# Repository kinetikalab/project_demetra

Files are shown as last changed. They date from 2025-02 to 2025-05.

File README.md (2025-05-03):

# Project Demetra

## Nitrogen Fixation in Gas Discharge: Fundamentals

### Historical Sketch
Attempts to use gas discharge to synthesize nitrogen fertilizers were made more than 100 years ago. The Birkeland-Eyde process used arc discharge to produce NO, which was then converted into nitric acid. 
However, the Birkeland-Eyde process lost competition to the Haber-Bosch process, as it consumed 60-80 kWh/kg N.

In recent years, interest in plasma-based nitrogen capture has been growing. While theoretical advancements have been made, the practical implementation of plasma-based methods remains close to the Birkeland-Eyde process in terms of energy efficiency and scalability.

The importance of more efficient, affordable, and sustainable nitrogen fertilizers cannot be overstated. The use of synthetic nitrogen fertilizers is directly responsible for sustaining nearly half of the world's population.

However, the Haber-Bosch process accounts for about 1-2% of global energy consumption and is responsible for 1-2% of greenhouse gas emissions from ammonia production and distribution alone. Moreover, the centralization of the nitrogen fertilizer market—primarily concentrated near natural gas extraction sites—reduces the resilience of food supply chains in developing countries, where both access to fertilizers and their efficient use remain major challenges.

This document describes a method to create a highly efficient plasma generator capable of synthesizing **NO3-** in water with energy efficiency comparable to the Haber-Bosch process.

### Step-by-Step process
Nitrogen is the primary component of air, comprising approximately 78% of its mass. However, the main challenge is that N₂ is an extremely strong and stable molecule due to its triple bond, which is difficult to break.

The triple bond is not only strong, but the cross-section of direct electron impact dissociation is negligible (due to certain quantum mechanical restrictions). That is why, for example, one can't find the N₂ dissociation cross-section in the LXCAT database.

Let's start at the end. We need the NO₃⁻ ion in liquid, which is obtained by oxidizing NO₂⁻, given a high concentration of O₃ and O₂.
NO₂⁻ is the product of HNO₂ dissociation in water. HNO₂ has medium solubility, but under certain conditions (described below), it can dissolve quite quickly:
```
HNO₂ → H⁺ + NO₂⁻
```
The fastest way to generate HNO₂ is:
```
NO + OH + M → HNO₂ + M, k = 2.16E-17, for N = 2.7E25 (a very fast reaction!)
```
So we need NO and OH.

Let's focus on NO. NO is the Holy Grail of nitrogen capture; all plasma-based nitrogen capture technologies somehow focus on NO production.

In the 1940s, Soviet physicist Zeldovich described in detail the formation of NO in an N₂/O₂ mixture via the following mechanism:
```
N₂ + O → NO + N, k = 3.0E-16 exp(-38300/T)  (1)

O₂ + N → NO + O, k = 4.5E-17 exp(-3272/T)   (2)
```
Under typical conditions in discharge channel (~1000–2000 K), reaction (2) is approximately million times faster. Most researchers focus on [2], but this is a trap.

N₂ is a highly stable molecule with a very strong triple bond. To break it, we need to supply two electrons to generate two N atoms:
```
N₂ +  e → N₂+ + 2e, Ee > 15.6 eV (rare in gas discharge)

N₂+ +  e → N + N
```
This drastically reduces overall energy efficiency, which is why the Birkeland–Eyde process lost to the Haber–Bosch process.

However, accelerating reaction [1] is not only possible but also relatively straightforward. Excited N₂ molecules, which are abundant in gas discharges, significantly enhance reaction [1].

For example, vibrational states with v > 7–8 accelerate [1] by up to 100,000 times, making it comparable to [2]

Finally, the most efficient way to break N₂ is:
```
N₂* + O → NO + N
```
with an additional bonus:
```
N + OH → NO + H
```
Thus, if we have excited N₂*, atomic oxygen, and OH, we can efficiently obtain two NO molecules.

Surprisingly, N₂* is not a problem in gas discharge, as about 50–70% of discharge energy is utilized for N₂ excitation. For an efficient Zeldovich reaction, vibrational levels of metastable A³ (and higher) states at 3–4+ are sufficient.

But the real challenge is oxygen. Atomic oxygen is obtained through the reaction:
```
O₂ + e⁻ → O(¹D) + O(³P), Eₑ > 8.4 eV
```
The second, more efficient reaction:
```
O₂ + e⁻ → O(³P) + O(³P), Eₑ > 6.2 eV
```
unfortunately has a significantly lower cross-section.

Taking into account that air consists of ~22% O₂ and 78% N₂, and that the N₂ excitation reaction consumes 2–3 times less energy than O₂ dissociation, we always face an oxygen deficit.

For every 5–6 N₂* molecules, we have only one O atom.

**Oxygen deficit is the main problem of plasma-based nitrogen capture.**

This statement is not entirely novel but is often overlooked in the literature.

To solve the oxygen deficit problem, we need a way to transfer energy from N₂* to O₂. Fortunately, we have one:
```
N₂(A³) + O₂ → O + O + N₂, k = 5E-18 × exp(-210/T)
```
This reaction is even more probable than the Zeldovich process, considering that O₂ concentration is much higher than O concentration. Approximately 70% of N₂(A³) reacts with O₂, generating atomic oxygen (while the remaining 30% produces O₂(a¹)).

The next question is: how can we direct more energy into N₂(A³) excitation rather than into N₂(v=1..5)?
BOLSIG+ provides a clear answer—increase the mean electron energy to 4–5 eV. For example, when the mean Eₑ = 2 eV, only 16% of the total discharge energy goes into N₂(A³) excitation, compared to 53% when Eₑ = 5 eV.

However, Eₑ > 5 eV is not typical in gas discharges at atmospheric pressure, because the self-consistent electric field directly limits electron energy.

**The final challenge – how to overcome the self-consistent electric field limitation?**

Surprisingly, the solution is relatively simple: introducing water vapor into the discharge zone at a concentration of approximately 30–40% of the total molecular content. This results in a humid, warm air stream at ~60–70°C.

However, this statement requires a more detailed explanation. Consider a simple drift-diffusion model.

**Continuity Equations**

Equation

where

Equation - electron and gas densities

Equation - ionization and attachment frequencies

**Flux Equations**

Equation 

where

Equation - diffusion and mobility coefficients

In a medium with a high concentration of H₂O molecules, the diffusion and mobility coefficients decrease significantly due to the high cross-section of rotational excitations in water molecules.

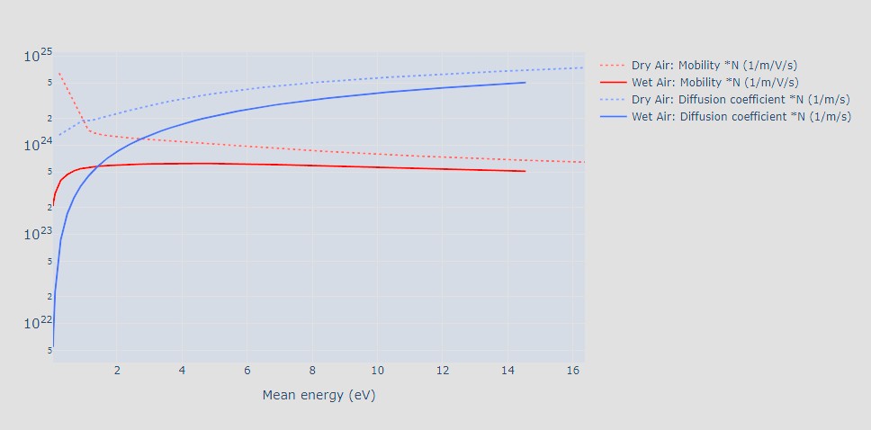
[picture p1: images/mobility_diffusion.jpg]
Diffusion and Mobility in Dry (0% H2O) and Wet Air (37% H2O) - BOLSIG+ Itikawa and Lison Databases


*Diffusion and Mobility in Dry [0% H2O] and Wet Air [37% H2O] - BOLSIG+ Itikawa and Lisbon Databases, including N₂ and O₂ rotational states*

From a physical intuition perspective, based on the **Continuity Equations**, electron density and the resulting self-consistent field are predominantly governed by ionization and attachment processes rather than by flux dynamics.

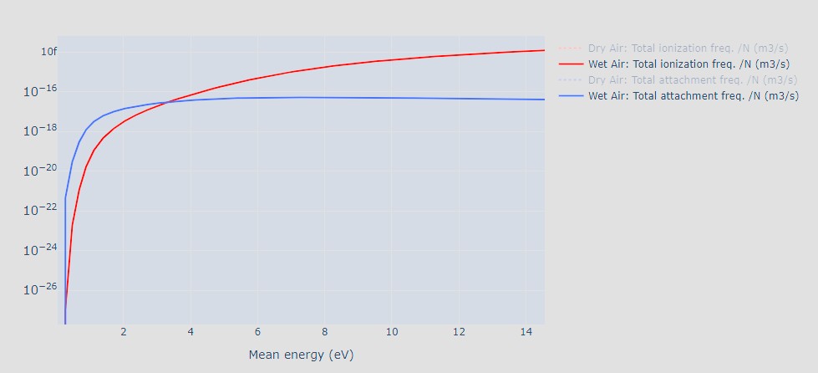
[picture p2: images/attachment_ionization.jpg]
Total Townsend Coefficients in Dry (0% H2O) and Wet Air (37% H2O) - BOLSIG+ Itikawa and Lison Databases


*Total Townsend Coefficients in Dry [0% H2O] and Wet Air [37% H2O] - BOLSIG+ Itikawa and Lisbon Databases, including N₂ and O₂ rotational states*

Fortunately, in heavily humidified air, the Townsend balance (i.e., the ratio of ionization to attachment rates) shifts favorably, with ionization exceeding attachment by a factor of 2–3 at approximately 5 eV.

As a result, in such an environment, the discharge naturally optimizes itself within the region of maximal NO generation efficiency.

**TBD – Demonstrate a 2D Plasma Drift-Diffusion model to prove physics intuition**

**Final Bonus**
In the presence of H₂O, O(¹D) predominantly generates OH radicals:
```
O(¹D) + H₂O → OH + OH
```
These OH molecules are crucial for the second NO capture step and HNO₂ synthesis.

That is the good explanation of high NO3- selectivity in heavy-humid air discharges.

### Collisional quenching

An important yet often overlooked concept in the literature is a simple strategy to mitigate the effects of collisional quenching.
Collisional quenching refers to the relaxation of excited molecular states through collisions with other particles. For example:

N₂(v=1) + M → N₂ + M

In such processes, the excitation energy is converted into heat due to collisions with neutral species.

This presents a significant challenge, particularly because nitrogen molecules (N₂) are typically excited not solely through direct electron impact, but predominantly via stepwise excitation processes:

N₂(v=1) + e⁻ → N₂(v=2) + e⁻
N₂(v=2) + e⁻ → N₂(v=3) + e⁻
N₂(v=3) + e⁻ → N₂(v=4) + e⁻
...

Each excitation step requires only ~0.2–0.3 eV of electron energy, meaning that the lower-energy tail of the electron energy distribution function (EEDF) can be utilized efficiently.

However, as previously noted, excited N₂ molecules are prone to loss through collisional quenching before they reach higher vibrational states. To counter this, a high electron density is required—ensuring that the likelihood of electron–molecule collisions increases and that molecules have a greater chance to undergo multiple excitation steps (typically 5–7) before being quenched.

**Thus, increasing electron density should significantly enhance nitrogen fixation efficiency by enabling successive vibrational excitations before quenching dominates.**

This insight naturally points toward the use of high-frequency discharges extended in space—such as high-frequency gliding arcs—as a promising approach to maximize vibrational excitation pathways.

## Energy Balance: Back-of-the-Napkin Estimate

Let's consider a discharge with a mean electron energy of **5 eV** in an **N₂/O₂/H₂O (50%/13%/37%)** mixture.  

According to the **BOLSIG+** solution:  
- **~16–19%** of the energy is spent on **O and O(¹D) generation**  
- **~16%** is spent on **N₂(v=2..5) excitation**  
- **~53%** is spent on **N₂(A³) excitation**  

On a weighted average:  
- **One N₂*** excitation costs **~2.6 eV**  
- **Atomic oxygen (O) costs ~3.2 eV** (close to the dissociation energy due to efficient energy transfer from **N₂*** to **O₂**)  
- **Two OH radicals cost ~3.8 eV** (calculated as **8.2/2 × 0.9**)  

Additional **OH** can be obtained through the **attachment process**:  

```
O₂ + e⁻ → O⁻ + O  
O⁻ + H₂O → OH⁻ + OH  
OH⁻ + e⁻ → OH + 2e⁻  
OH⁻ + O₂⁺/N₂⁺ → OH + O₂/N₂  
```

The overall energy consumption **~10 kWh/kg of N (bottom line)**.

## Key Lessons Learned
For efficient NO2-/NO3- capture from the air, the following conditions must be met:
1. Discharge in Hot, Humid Air.
2. Efficient mixing to saturate the water with oxygen and ensure rapid dissolution of HNO2 and NO₂⁻ oxidation.
3. Optimized Discharge Chamber Design: On the one hand, it must prevent hot arcs, and on the other, it should not include a dielectric barrier to avoid discharge initiation losses.

## Basic Design Principles

1. **Ignition of Gas Discharge in air-vapor mixture**

2. **Stable Thermal Discharge for Energy Efficiency**: To ensure energy efficiency, a stable non-thermal and non-DBD discharge must be used, such as a gliding arc or streamer discharge (which are alse increase electron density and launch step-by-step excutation)

3. **Minimization of Byproduct Losses**: Once the N2 molecule is dissociated, byproducts such as NO2, N2O5, NO3, and N2O must be recirculated into the discharge to regenerate NO (refer to the Secondary Reactions section).

4. **Efficient mixing water with gas discharge products**: Ensuring HNO2 dissolution and enrich the water with O₂.

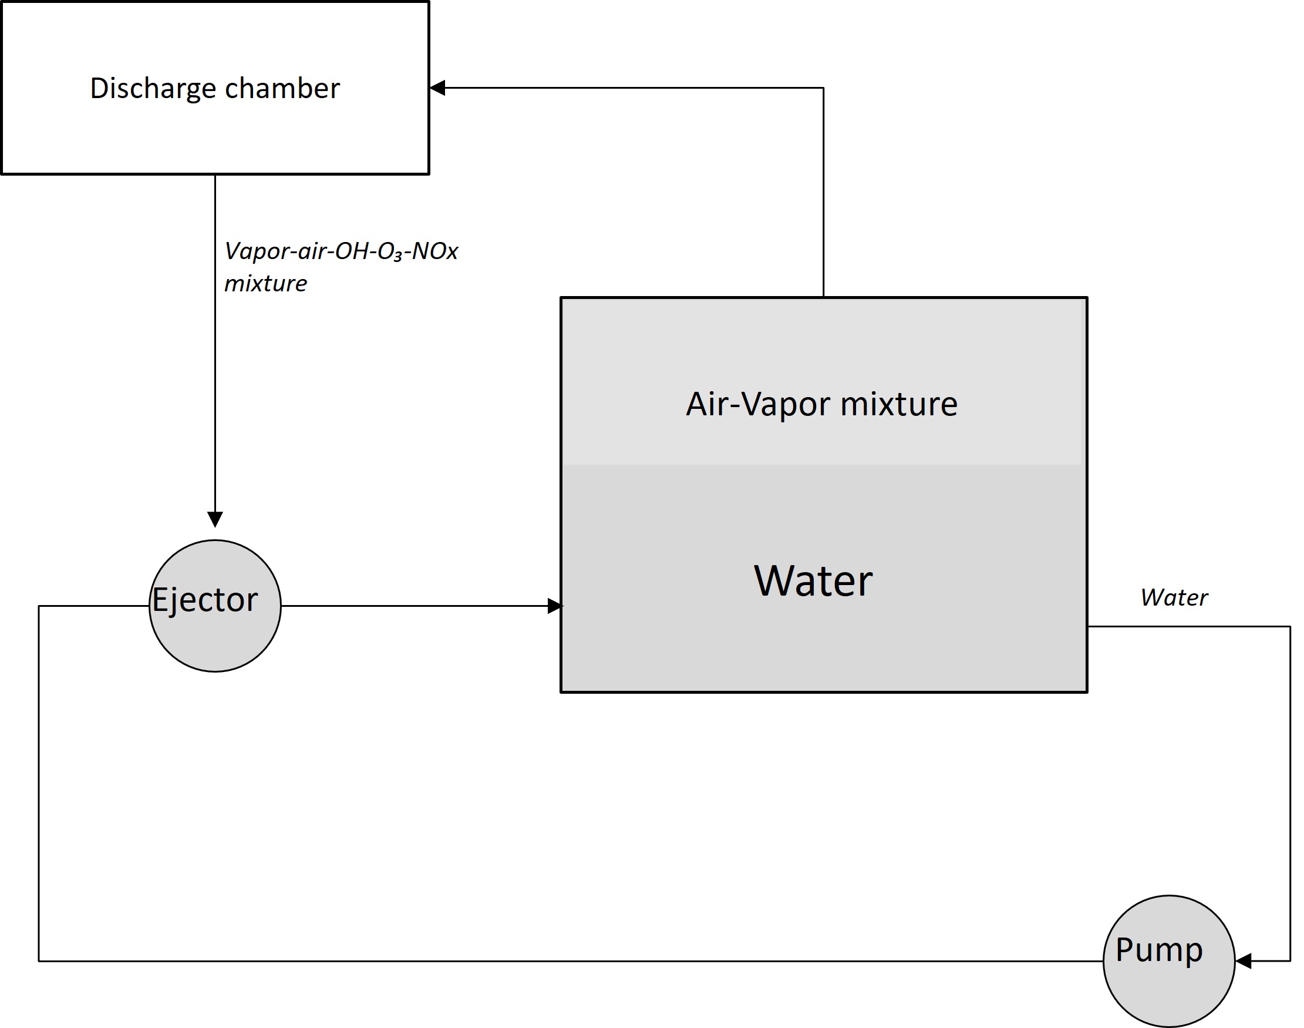
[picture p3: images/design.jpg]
Schematic Design


A spiral gliding arc is used [discharge_chambers](./discharge_chambers/).

## Latest Experimental Results
**Date:** May 3, 2025

- **Power Consumption:** 60 W (pump) + 76 W (discharge)
- **Treatment Time:** 3 minutes
- **Volume:** 1.5 L

**Measured Concentrations:**  
- **NO2-:** 0-1 ppm (approximate, pending verification with IC)  
- **NO3-:** ~400 ppm (measured by HORBA NO3- ISE, pending verification with IC)

**Energy Efficiency:**
- **Discharge:** ~56 kWh/kg N. However estimated losses of the H-Bridge due to low power ~20-30 W, i.e real plasma results ~25-30 kWh/kg N

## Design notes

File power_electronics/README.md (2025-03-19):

# Description

Here is the power electronics design. 

Read the [equivalent_circuit](equivalent_circuit) first, and then you will have a better understanding of the key components: the [transformer](transformer) and the [H-bridge](h-bridge).

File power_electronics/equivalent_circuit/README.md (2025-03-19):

# Description

This is a simplified LTSPICE model of power electronics. 

The H-bridge is substituted by an AC power supply for simplicity (for the detailed design of the H-bridge, see the [h-bridge](/power_electronics/h-bridge) folder).

### Key Components:

- **C1**: Balance capacitor battery.
- **Ls1**: Primary leakage inductance.
- **Ls2**: Secondary leakage inductance.
- **Lm1**: Primary magnetizing inductance.
- **Lm2**: Secondary magnetizing inductance.
- **k**: Coupling factor. Learn how to measure it [here](https://electronics.stackexchange.com/questions/596093/how-to-measure-coupling-coefficient).
- **R1**: Resistance of the secondary winding.
- **Cd**: Capacity of the discharge chamber.
- **Rd**: Resistance of the discharge chamber (theoretical infinity, but in discharge breakdown ~100 kΩ).
- **Cp**: Parasitic capacity (secondary winding).
- **Cw**: Parasitic capacity (Inter-winding).

### Additional Information:

- For more information on the H-bridge design, please refer to the [h-bridge](/power_electronics/h-bridge) folder.
- For detailed transformer design, check the [transformer](/power_electronics/transformer) folder.

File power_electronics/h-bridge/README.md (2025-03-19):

# Description

Complete design documentation for a high-voltage power H-bridge.

The design is highly stable, capable of operating at frequencies up to **1 MHz**, and generates approximately **2 kV**. 

With a properly designed transformer (see [transformer](/power_electronics/transformer/)), this can reach **30-60 kV** in the discharge chamber.

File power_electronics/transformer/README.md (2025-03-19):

# Description

Design of a high-voltage resonant transformer (L1-L2). See the equivalent circuit diagram in [equivalent_circuit](/power_electronics/equivalent_circuit).

The current coupling coefficient achieved is **k = 0.99**.

- **Secondary winding parasitic capacitance:** 11 pF  
- **Interwinding parasitic capacitance:** 10 pF  

## Design

### Materials Needed

1. Nanocrystal core: [T60006-L2090-W518 Vacuumschmelze](https://eu.mouser.com/ProductDetail/Vacuumschmelze/T60006-L2090-W518?qs=ePbE9GiMmvUhadR4ky1MIg%3D%3D)
2. Coated copper wire: [0.3 mm](https://www.amazon.de/-/en/dp/B09VP9QQGW?ref=ppx_yo2ov_dt_b_fed_asin_title)
3. Housing: [CAD model](/power_electronics/transformer/High-Voltage_Transformer.f3d)
4. Potting compound 
5. Litz wire for primary windings (I used 3x20x0.2 mm wire)

### Process
See transformer design [CAD Model](/power_electronics/transformer/High-Voltage_Transformer.f3d)
**Insulation of the core**
1. Put core intto filling form (do no forget add silcon overaly)
2. Fill the form with potting compound and wait until it cure. 
It is important to avoid core breakdown.
**Secondary windings**
3. Wind the secondary winding using 0.3 mm coated wire, approximately 130 turns.  
   **IMPORTANT:** Maintain a spacing of ~0.2–0.3 mm between turns to minimize parasitic capacitance.
4. Fill the seondary winding with potting compound and wait until it cure.
**Primary windings**
5. Wind 3 primary windings. Refer to the provided 3D model for detailed instructions.

## Comments

1. The T60006-L2090-W518 core is used because it has very low losses and ensures exceptional magnetic permeability. This allows for **fewer turns**, which reduces parasitic capacitance.
2. Litz wire, or even a bundle of Litz wires, is essential due to the high current in the primary windings. It minimizes the skin effect and improves efficiency.
3. Potting compound is critical for insulation to prevent breakdowns between the secondary and primary windings or core breakdown.

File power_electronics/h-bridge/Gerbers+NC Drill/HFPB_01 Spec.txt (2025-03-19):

HFPB_01 Specifications:

Board size: 125mm x 200mm
Board area: 2.5 dm^2
Material: Green FR4, lead free RoHs (with dielectric constant 4.2-4.6)
Board Thickness: 1.5mm
Number of Layers: 8

Top/bottom copper thickness: 35um (1.0 oz)

Minimum width of Traces: 0.2mm
Minimum spacing between Traces: 0.2mm
Minimum VIA diameters: 0.3mm
Minimum band width around VIA: 0.15mm

Stackup settings:
________________
Gerber - Content
________________
.GTP - Top paste
.GTO - Top silkscreen (white)
.GTS - Top solder mask
.GTL - Top copper
	PRE-PREG (0.125mm)
.G1 - Inner copper 1
	CORE FR4 (0.2mm)
.G2 - Inner copper 2
	PRE-PREG (0.2mm)
.G3 - Inner copper 3
	CORE (0.2mm)
.G4 - Inner copper 4
	PRE-PREG (0.2mm)
.G5 - Inner copper 5
	CORE (0.2mm)
.G6 - Inner copper 6
	PRE-PREG (0.125mm)
.GBL - Bottom copper
.GBS - Bottom solder mask
.GBO - Bottom silkscreen (white)
.GBP - Bottom paste

.GM1 - Board outline

HFPB_01-PCB-RoundHoles.TXT - Round holes coordinates, sizes
HFPB_01-PCB-SlotHoles.TXT - Slot holes coordinates, sizes

Plating: ImmersGold
Machining: Milling 1mm diameter cutter or smaller

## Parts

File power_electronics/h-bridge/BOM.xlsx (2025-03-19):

Part Number: |  |  |  |  |  | Date:
Rev: |  | 01 |  |  |  | 2021 May 25
Associated Board: |  | HFPB_01-PCB
Description: |  | High Frequency Power Bridge HFPB. Bill of materials |  |  |  | Moscow
Item | Reference | Part number | D Sh | Vendor | Package/case | Description | Quant per 1 PCB | Price per 1p (Mous. for rus) | Total cost | Comment | Digi-key | Mouser | Other distributors
 | I n t e g r a t e d c i r c u i t
1 | U1 | TSR 1-24120 | D (https://www.tracopower.com/sites/default/files/products/datasheets/tsr1_datasheet.pdf) | Traco | SIP-3 | DC/DC Converter, Non-Iso, Uout=12V, Iout=1A | 1 | 8.67 | 8.670 |  | 1951-2739-ND (https://www.digikey.com/en/products/detail/traco-power/TSR-1-24120/9383773) | 495-TSR-1-24120 (https://ru.mouser.com/ProductDetail/TRACO-Power/TSR-1-24120?qs=ckJk83FOD0XFyuKFnkiJHw%3D%3D) | Elitan (https://www.elitan.ru/price/index.php?find=TSR1-24120&delay=-1&mfg=all&seenform=y)
2 | U2 | TSR 1-2450 | D (https://www.tracopower.com/sites/default/files/products/datasheets/tsr1_datasheet.pdf) | Traco | SIP-3 | DC/DC Converter, Non-Iso, Uout=5.0V, Iout=1A | 1 | 8.67 | 8.670 |  | 1951-2747-ND (https://www.digikey.com/en/products/detail/traco-power/TSR-1-2450/9383780) | 495-TSR-1-2450 (https://ru.mouser.com/ProductDetail/TRACO-Power/TSR-1-2450?qs=ckJk83FOD0XFKqda0Mzkgw%3D%3D) | Elitan (https://www.elitan.ru/price/index.php?find=TSR1-2450&delay=-1&mfg=all&seenform=y)
3 | U3 | LD39050PU33R | D (https://www.st.com/content/ccc/resource/technical/document/datasheet/12/43/cc/93/21/f6/41/66/CD00227527.pdf/files/CD00227527.pdf/jcr:content/translations/en.C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) | STM | DFN-6 | LDO 3.3V 500mA | 1 | 1.87 | 1.870 |  | 497-8716-1-ND (https://www.digikey.com/en/products/detail/stmicroelectronics/LD39050PU33R/2039876) | 511-LD39050PU33R (https://ru.mouser.com/ProductDetail/STMicroelectronics/LD39050PU33R) | Elitan (https://www.elitan.ru/price/index.php?find=LD39050PU33R&delay=-1&mfg=all&seenform=y)
4 | U4 | STM32F334R8T7 | D (https://www.st.com/content/ccc/resource/technical/document/datasheet/d1/cd/3d/18/a2/2c/4e/d0/DM00097745.pdf/files/DM00097745.pdf/jcr:content/translations/en.D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) | STM | LQFP-64 | ARM Cortex-M4 STM32F3 IC 32-Bit 72MHz 64KB | 1 | 11.62 | 11.620 |  | 497-18933-ND (https://www.digikey.com/en/products/detail/stmicroelectronics/STM32F334R8T7/5268274) | 511-STM32F334R8T7 (https://ru.mouser.com/ProductDetail/STMicroelectronics/STM32F334R8T7?qs=9MuLHSklicpmYDk0V9oFMQ%3D%3D) | Elitan (https://www.elitan.ru/price/index.php?find=STM32F334R8T7&delay=-1&mfg=all&seenform=y)
5 | U5 | AD8628AUJZ | D (https://www.analog.com/media/en/technical-documentation/data-sheets/AD8628_8629_8630.pdf) | Analog | TSOT23-5 | OpAmp Rail-to-Rail 1 Channel | 1 | 4.27 | 4.270 |  | AD8628AUJZ-REEL7CT-ND (https://www.digikey.com/en/products/detail/analog-devices-inc/AD8628AUJZ-REEL7/996267) | 584-AD8628AUJZ-R7 (https://ru.mouser.com/ProductDetail/Analog-Devices/AD8628AUJZ-REEL7?qs=%2FtpEQrCGXCwiRJmva1wT4g%3D%3D) | Elitan (https://www.elitan.ru/price/index.php?find=AD8628AUJZ&delay=-1&mfg=all&seenform=y)
6 | U6 | CP2102-GM | D (https://www.silabs.com/documents/public/data-sheets/CP2102-9.pdf) | Silicon Labs | QFN-28 | Interface USB to UART | 1 | 5.13 | 5.130 |  | 336-1160-5-ND (https://www.digikey.com/en/products/detail/silicon-labs/CP2102-GM/696598) | 634-CP2102-GM (https://ru.mouser.com/ProductDetail/Silicon-Labs/CP2102-GM?qs=yHCtFi5ROqJvCcyR88R4Pg%3D%3D) | Elitan (https://www.elitan.ru/price/index.php?find=CP2102-GM&delay=-1&mfg=all&seenform=y)
7 | U7 | ISO1540D | D (https://www.ti.com/lit/ds/symlink/iso1540-q1.pdf?ts=1615839581838) | Silicon Labs | SOIC-8 | Digital Isolator I2C 2500Vrms 2 Channel 1Mbps | 1 | 9.29 | 9.290 |  | 296-34896-5-ND (https://www.digikey.com/en/products/detail/texas-instruments/ISO1540D/3601070) | 595-ISO1540D (https://ru.mouser.com/ProductDetail/Texas-Instruments/ISO1540D?qs=rg6Iqu58vpWvO86XnJi3%2Fg%3D%3D) | Elitan (https://www.elitan.ru/price/index.php?find=ISO1540D&delay=-1&mfg=all&seenform=y)
8 | U8, U11, U20, U21 | EC4SAW-24S15N | D (https://www.cincon.com/productdownload/SPEC-EC4SAW-V12.pdf,%20https:/www.cincon.com/productdownload/EC4SAW-SERIES-application-note.pdf) | Cincon | SIP-8 | DC/DC Converter 6W 1.5kV Isolated | 4 | 18.61 | 74.440 |  | EC4SAW-24S15N (https://www.digikey.com/en/products/detail/cincon-electronics-co-ltd/EC4SAW-24S15N/9683268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) | 418-EC4SAW-24S15N (https://ru.mouser.com/ProductDetail/Cincon/EC4SAW-24S15N) | Elitan (https://www.elitan.ru/price/index.php?find=EC4SAW-24S15N&delay=-1&mfg=all&seenform=y)
9 | U9, U10, U22, U23 | TPS71550DCKR | D (https://www.ti.com/lit/ds/symlink/tps715.pdf?HQS=dis-dk-null-digikeymode-dsf-pf-null-wwe&ts=1615331244877) | Texas | SC70-5 | LDO 3.3V 50mA | 4 | 1.2 | 4.800 |  | 296-15046-1-ND (https://www.digikey.com/en/products/detail/texas-instruments/TPS71550DCKR/562815) | 595-TPS71550DCKR (https://ru.mouser.com/ProductDetail/Texas-Instruments/TPS71550DCKR?qs=Gse6rAGbi7%252BvaZj1yCtdfw%3D%3D) | Elitan (https://www.elitan.ru/price/index.php?find=TPS71550DCKR&delay=-1&mfg=all&seenform=y)
10 | U12, U13, U16, U17 | SI8620BC-B-ISR | D (https://www.silabs.com/documents/public/data-sheets/si861x-2x-datasheet.pdf) | Silicon Labs | SOIC-8 | Digital Isolator 3750Vrms 2 Channel 150Mbps | 4 | 2.01 | 8.040 |  | 336-4330-1-ND (https://www.digikey.com/en/products/detail/silicon-labs/SI8620BC-B-ISR/4069784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) | 634-SI8620BC-B-ISR (https://ru.mouser.com/ProductDetail/Silicon-Labs/SI8620BC-B-ISR) | Elitan (https://www.elitan.ru/price/index.php?find=SI8620&delay=-1&mfg=all&seenform=y)
11 | U14, U15, U18, U19 | IXDD614YI | D (https://www.ixysic.com/home/pdfs.nsf/0/18AB54BEE23C4E71852577520051C399/$file/IXD_614.pdf) | IXYS | TO263-5 | MOSFET Driver IC | 4 | 8.85 | 35.400 |  | CLA338-ND (https://www.digikey.com/en/products/detail/ixys-integrated-circuits-division/IXDD614YI/2391600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) | 849-IXDD614YI (https://ru.mouser.com/ProductDetail/IXYS-Integrated-Circuits/IXDD614YI/) | Elitan (https://www.elitan.ru/price/index.php?find=IXDD614YI&delay=-1&mfg=all&seenform=y)
 | Alternative | IXDD630YI | D (https://www.ixysic.com/home/pdfs.nsf/0/6AC7CC624179BDA185257873005D6BE4/$file/IXD_630.pdf) | IXYS | TO263-5 | MOSFET Driver IC | 4 | 13.5 |  |  | CLA375-ND (https://www.digikey.com/en/products/detail/ixys-integrated-circuits-division/IXDD630YI/2623251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) | 849-IXDD630YI (https://ru.mouser.com/ProductDetail/IXYS-Integrated-Circuits/IXDD630YI?qs=uhAJVUz%252BE38ko%2Fiwob07zA%3D%3D)
 | I n d u c t o r s
12 | FB1-FB17 | MPZ1608S601ATA00 | D (https://product.tdk.com/info/en/catalog/datasheets/beads_commercial_power_mpz1608_en.pdf) | TDK | SMD0603 | Ferrite Bead 600Ohms 1A 150mOhm | 17 | 0.163 | 2.771 |  | 445-2205-1-ND (https://www.digikey.com/product-detail/en/tdk-corporation/MPZ1608S601ATA00/445-2205-1-ND/765103) | 810-MPZ1608S601ATA00 (https://ru.mouser.com/ProductDetail/TDK/MPZ1608S601ATA00)
13 | L1, L2, L3, L4 | DLW5BTM142TQ2L | D (https://www.murata.com/en-us/products/productdata/8796761587742/EFLC0025.pdf) | Murata | SMD-4 | Common Mode Choke 2 lines 1.4kOhm 2A 56mOhm | 4 | 2.16 | 8.640 |  | 490-11110-1-ND (https://www.digikey.com/en/products/detail/murata-electronics/DLW5BTM142TQ2L/4421377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) | 81-DLW5BTM142TQ2L (https://ru.mouser.com/ProductDetail/Murata-Electronics/DLW5BTM142TQ2L?qs=eTNEoJdcnEJfMtnluA8TOg%3D%3D)
 | L E D s
14 | LD1 | LTST-C193KGKT-5A | D (http://optoelectronics.liteon.com/upload/download/DS22-2007-0094/LTST-C193KGKT-5A.PDF) | Lite-On Inc. | SMD0603 | LED Green 5mA 572nm Vf=2.0V (≈) | 1 | 0.632 | 0.632 |  | 160-1828-1-ND (https://www.digikey.com/product-detail/en/lite-on-inc/LTST-C193KGKT-5A/160-1828-1-ND/2356247) | 859-LTSTC193KGKT5A (https://ru.mouser.com/ProductDetail/Lite-On/LTST-C193KGKT-5A)
15 | LD2, LD5, LD6 | LTST-C193KSKT-5A | D (https://optoelectronics.liteon.com/upload/download/DS22-2004-141/LTST-C193KSKT-5A.PDF) | Lite-On Inc. | SMD0603 | LED Yellow 5mA 591nm Vf=2.0V (≈) | 3 | 0.632 | 1.896 |  | 160-1831-1-ND (https://www.digikey.com/en/products/detail/lite-on-inc/LTST-C193KSKT-5A/2356245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) | 859-LTSTC193KSKT5A (https://ru.mouser.com/ProductDetail/Lite-On/LTST-C193KSKT-5A)
16 | LD3 | LTST-C194KFKT | D (https://optoelectronics.liteon.com/upload/download/DS22-2010-0196/LTST-C194KFKT.PDF) | Lite-On Inc. | SMD0603 | LED Orange 5mA 605nm Vf=2.0V (≈) | 1 | 0.632 | 0.632 |  | 160-1833-1-ND (https://www.digikey.com/en/products/detail/lite-on-inc/LTST-C194KFKT/2356222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) | 859-LTST-C194KFKT (https://ru.mouser.com/ProductDetail/Lite-On/LTST-C194KFKT)
17 | LD4 | LTST-C193KRKT-5A | D | Lite-On Inc. | SMD0603 | LED Red 5mA 631nm Vf=2.0V (≈) | 1 | 0.632 | 0.632 |  | 160-1830-1-ND (https://www.digikey.com/en/products/detail/lite-on-inc/LTST-C193KRKT-5A/2356244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) | 859-LTSTC193KRKT5A (https://ru.mouser.com/ProductDetail/Lite-On/LTST-C193KRKT-5A)
 | D i o d e s
18 | D1, D7, D10, D11, D14, D15 | BAT54J,115 | D (https://rocelec.widen.net/view/pdf/es9ugfukaw/PHGLS14913-1.pdf?t.download=true&u=5oefqw) | Nexperia | SOD-323F | Diode Schottky 30V 0.2A | 6 | 0.567 | 3.402 |  | 1727-4818-1-ND (https://www.digikey.com/en/products/detail/nexperia-usa-inc/BAT54J-115/1692654) | 771-BAT54J115 (https://ru.mouser.com/ProductDetail/Nexperia/BAT54J115)
19 | D2, D12, D13, D16, D17 | MBRS540T3G | D (https://www.onsemi.com/pdf/datasheet/mbrs540t3-d.pdf) | ON Semi | SMC | Diode Schottky 40V 5A | 5 | 0.94 | 4.700 |  | MBRS540T3GOSCT-ND (https://www.digikey.com/en/products/detail/on-semiconductor/MBRS540T3G/918647) | 863-MBRS540T3G (https://ru.mouser.com/ProductDetail/ON-Semiconductor/MBRS540T3G)
20 | D3, D4 | BAT60JFILM | D (https://www.st.com/content/ccc/resource/technical/document/datasheet/3d/d2/27/1d/20/e3/4d/48/CD00001944.pdf/files/CD00001944.pdf/jcr:content/translations/en.C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) | STM | SOD-323 | Diode Schottky 10V 3A | 2 | 0.649 | 1.298 |  | 497-3707-1-ND (https://www.digikey.com/en/products/detail/stmicroelectronics/BAT60JFILM/686386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) | 511-BAT60JFILM (https://ru.mouser.com/ProductDetail/STMicroelectronics/BAT60JFILM)
21 | D5, D6, D8 | D1213A-01T-7 | D (https://www.diodes.com/assets/Datasheets/D1213A-01T.pdf) | Diodes Inc. | SOD-523 | TVS Diode Vstand=5.5V Vclamp=10V | 3 | 0.617 | 1.851 |  | D1213A-01T-7DICT-ND (https://www.digikey.com/en/products/detail/diodes-incorporated/d1213a-01t-7/3340396) | 621-D1213A-01T-7 (https://ru.mouser.com/ProductDetail/Diodes-Incorporated/D1213A-01T-7)
22 | D9 | TPD2E001DZDR | D (https://www.ti.com/lit/ds/symlink/tpd2e001.pdf?HQS=dis-dk-null-digikeymode-dsf-pf-null-wwe&ts=1616116107965) | Texas | SOP-4 | TVS Diode Vstand=5.5V Vbr=11V | 1 | 1.02 | 1.020 |  | 296-24770-1-ND (https://www.digikey.com/en/products/detail/texas-instruments/TPD2E001DZDR/1907454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) | 595-TPD2E001DZDR (https://ru.mouser.com/ProductDetail/Texas-Instruments/TPD2E001DZDR)
 | B u z z e r
23 | LS1 | CMI-9605IC-0580T | D (https://www.mouser.fi/datasheet/2/670/cmi-9605ic-0580t-1777058.pdf) | CUI | Thr.holes 9.6x5.0 | Buzzer Magnetic 5V 80dB 2.7kHz | 1 | 2.28 | 2.280 |  | 2223-CMI-9605IC-0580T-ND (https://www.digikey.com/product-detail/en/cui-devices/CMI-9605IC-0580T/2223-CMI-9605IC-0580T-ND/11674175) | 490-CMI-9605IC-0580T (https://ru.mouser.com/ProductDetail/CUI-Devices/CMI-9605IC-0580T)
 | S w I t c h
24 | BR1 | PEC11H-4020F-S0016 | D (https://www.bourns.com/docs/Product-Datasheets/PEC11H.pdf) | Bourns | Thr. Hole | Encoder Mechanical 16 PPR | 1 | 4.4 | 4.400 |  | 118-PEC11H-4020F-S0016-ND (https://www.digikey.com/en/products/detail/bourns-inc/PEC11H-4020F-S0016/12349534) | 652-PEC11H4020FS0016 (https://ru.mouser.com/ProductDetail/Bourns/PEC11H-4020F-S0016)
25 | BU1, BU2, BU3, BU4 | 1571563-8 | D | TE Conn. | SMD 6.0x6.00 | Switch tactile OFF-(ON) 6.0x6.0x5.0mm | 4 | 0.552 | 2.208 |  | 450-2056-1-ND (https://www.digikey.com/product-detail/en/te-connectivity-alcoswitch-switches/1571563-8/450-2056-1-ND/4569746) | 506-1571563-8 (https://ru.mouser.com/ProductDetail/TE-Connectivity-PB/1571563-8)
26 | SW1 | EG2208A | D (https://sten-eswitch-13110800-production.s3.amazonaws.com/system/asset/product_line/data_sheet/119/EG.pdf) | E-Switch | Thr. Hole, Right Ang. | Switch ON-ON 0.3A 50V | 1 | 1.12 | 1.120 |  | EG1942-ND (https://www.digikey.com/en/products/detail/e-switch/EG2208A/301964?s=N4IgTCBcDaIKIHExgAwA4CCIC6BfIA) | 612-EG2208A (https://ru.mouser.com/ProductDetail/E-Switch/EG2208A)
 | T r a n s I s t o r s
27 | Q1, Q3, Q5 | IRLML6244TRPBF | D (https://www.infineon.com/dgdl/irlml6244pbf.pdf?fileId=5546d462533600a4015356686fed261f) | Infineon | SOT23-3 | MOSFET N-channel, 20V, 6.3A, 21mOhm | 3 | 0.65 | 1.950 |  | IRLML6244TRPBFCT-ND (https://www.digikey.com/en/products/detail/infineon-technologies/IRLML6244TRPBF/2393871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) | 942-IRLML6244TRPBF (https://ru.mouser.com/ProductDetail/Infineon-IR/IRLML6244TRPBF)
28 | Q2, Q4 | DMC2400UV-7 | D (https://www.diodes.com/assets/Datasheets/DMC2400UV.pdf) | Diodes Inc. | SOT-563 | MOSFETs N and P-channel (Dual); 20V, 1A; ESD protected | 2 | 0.65 | 1.300 |  | DMC2400UV-7DICT-ND (https://www.digikey.com/product-detail/en/diodes-incorporated/DMC2400UV-7/DMC2400UV-7DICT-ND/2918407) | 21-DMC2400UV-7 (https://ru.mouser.com/ProductDetail/Diodes-Incorporated/DMC2400UV-7)
29 | Q6-Q13 | IXTH240N15X4 | D (https://www.littelfuse.com/~/media/electronics/datasheets/discrete_mosfets/littelfuse_discrete_mosfets_n-channel_ultra_junction_ixt_240n15x4_datasheet.pdf.pdf) | IXYS | TO247-3 | MOSFET N-chanel, 150V, 240A, 4.4mOhm | 8 | 19.15 | 153.200 |  | IXTH240N15X4-ND (https://www.digikey.com/en/products/detail/ixys/IXTH240N15X4/10222203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) | 747-IXTH240N15X4 (https://ru.mouser.com/ProductDetail/IXYS/IXTH240N15X4?qs=T3oQrply3y%252BbuTinOhn9MQ%3D%3D)
 | Alternative | IRFP3077PbF | D (https://www.infineon.com/dgdl/irfp3077pbf.pdf?fileId=5546d462533600a401535628cd701fee) | IXYS | TO247-3 | MOSFET N-chanel, 75V, 200A, 2.8mOhm | 8 | 8 |  |  | IRFP3077PbF (https://www.digikey.com/en/products/detail/infineon-technologies/IRFP3077PBF/1894148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) | 942-IRFP3077PBF (https://ru.mouser.com/ProductDetail/Infineon-IR/IRFP3077PBF)
 | C r y s t a l
30 | Y1 | ECS-80-20-5PX-TR | D (https://ecsxtal.com/store/pdf/csm-7x.pdf) | ECS Inc. | HC-49/US | Crystal 8MHz 20pF 30ppm | 1 | 0.44 | 0.440 |  | XC2076CT-ND (https://www.digikey.com/product-detail/en/ecs-inc/ECS-80-20-5PX-TR/XC2076CT-ND/5875560) | 520-80-20-5PX-T (https://ru.mouser.com/ProductDetail/ECS/ECS-80-20-5PX-TR?qs=wYonFgBYHKlzFXpOtPA%2FIw%3D%3D)
 | C a p a c i t o r
31 | C1, C14, C38, C83, C84, C88, C91, C128, C129, C131, C134 | C1210C106M6PACTU | D (https://content.kemet.com/datasheets/KEM_C1006_X5R_SMD.pdf) | KEMET | SMD1210 | Ceramic 10uF 20% X5R 35V | 11 | 2.66 | 29.260 |  | 399-5509-1-ND (https://www.digikey.com/en/products/detail/kemet/C1210C106M6PACTU/1950669) | 80-C1210C106M6P (https://ru.mouser.com/ProductDetail/KEMET/C1210C106M6PACTU)
32 | C2, C8, C82, C85, C127, C130 | GRT188R61H105KE13D | D (https://search.murata.co.jp/Ceramy/image/img/A01X/G101/ENG/GRT188R61H105KE13-01.pdf) | Murata | SMD0603 | Ceramic 1uF 10% X5R 50V | 6 | 0.42 | 2.520 |  | 490-12330-1-ND (https://www.digikey.com/en/products/detail/murata-electronics/GRT188R61H105KE13D/5416752) | 81-GRT188R61H105KE3D (https://ru.mouser.com/ProductDetail/Murata-Electronics/GRT188R61H105KE13D)
33 | C3, C9 | C0603C104K5RAC7082 | D (https://content.kemet.com/datasheets/KEM_C1002_X7R_SMD.pdf) | KEMET | SMD0603 | Ceramic 0.1uF 10% X7R 50V | 2 | 0.42 | 0.840 |  | 399-C0603C104K5RAC7082CT-ND (https://www.digikey.com/en/products/detail/kemet/C0603C104K5RAC7082/12701309) | 80-C0603C104K5R7082 (https://ru.mouser.com/ProductDetail/KEMET/C0603C104K5RAC7082)
34 | C4, C12, C17, C21, C28, C80, C81, C100, C103, C116, C119, C125, C126 | C1608X7R1E105K080AB | D (https://product.tdk.com/en/system/files) | TDK | SMD0603 | Ceramic 1uF 10% X7R 25V | 13 | 0.32 | 4.160 |  | 445-5956-1-ND (https://www.digikey.com/en/products/detail/tdk-corporation/C1608X7R1E105K080AB/2443434) | 810-C1608X7R1E105K (https://ru.mouser.com/ProductDetail/TDK/C1608X7R1E105K080AB)
35 | C5, C6 | RL81V101MDN1KX | D (http://nichicon-us.com/english/products/pdfs/e-rl8.pdf) | Nichicon | Radial, T/H 8.0x8.0 | Polymer Radial 100µF 20% 35V 25mOhm 2000h | 2 | 3.27 | 6.540 |  | 493-6630-1-ND (https://www.digikey.com/product-detail/en/nichicon/RL81V101MDN1KX/493-6630-1-ND/3466042) | 647-RL81V101MDN1KX (https://ru.mouser.com/ProductDetail/Nichicon/RL81V101MDN1KX)
 | Alternative | JRB1V221M03500800120000B | D (https://static.chipdip.ru/lib/762/DOC005762382.pdf) | JB | Radial, T/H 8.0x12.0 | Eletrolytic Radial 220µF 20% 35V 2000h | 2 | 0.1
36 | C7, C13, C15, C19, C20, C26, C30, C40, C43, C45, C46, C47, C48, C49, C94, C95, C110, C111, C124 | GRM1885C1H103JA01D | D (https://www.murata.com/-/media/webrenewal/support/library/catalog/products/capacitor/ceramiccapacitor/c02e.ashx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) | Murata | SMD0603 | Ceramic 0.01uF 5% NP0 50V | 19 | 0.31 | 5.890 |  | 490-9666-1-ND (https://www.digikey.com/en/products/detail/murata-electronics/GRM1885C1H103JA01D/4421555) | 81-GRM1885C1H103JA1D (https://ru.mouser.com/ProductDetail/Murata-Electronics/GRM1885C1H103JA01D)
37 | C10, C25, C34 | C1210C107M8PACTU | D (https://content.kemet.com/datasheets/KEM_C1006_X5R_SMD.pdf) | KEMET | SMD1210 | Ceramic 100uF 20% X5R 10V | 3 | 4.23 | 12.690 |  | 399-11631-1-ND (https://www.digikey.com/en/products/detail/kemet/C1210C107M8PACTU/4918884) | 80-C1210C107M8P (https://ru.mouser.com/ProductDetail/KEMET/C1210C107M8PACTU)
38 | C11 | RL81C331MDN1KX | D (https://www.nichicon.co.jp/english/products/pdfs/e-rl8.pdf) | Nichicon | Radial, T/H 9.0x8.0 | Polymer Radial 330µF 20% 16V 12mOhm 2000h | 1 | 1.51 | 1.510 |  | 493-6629-1-ND (https://www.digikey.com/en/products/detail/nichicon/RL81C331MDN1KX/3466040) | 647-RL81C331MDN1KX (https://ru.mouser.com/ProductDetail/Nichicon/RL81C331MDN1KX)
39 | C16, C18, C22, C23, C24, C27, C29, C31, C32, C33, C35, C36, C37, C39, C44, C86, C87, C92, C93, C101, C102, C105, C106, C108, C109, C117, C118, C121, C122, C135, C136 | C0603C104K3RAC7082 | D (https://content.kemet.com/datasheets/KEM_C1002_X7R_SMD.pdf) | KEMET | SMD0603 | Ceramic 0.1uF 10% X7R 25V | 31 | 0.32 | 9.920 |  | 399-C0603C104K3RAC7082CT-ND (https://www.digikey.com/en/products/detail/kemet/C0603C104K3RAC7082/12700954) | 80-C0603C104K3R7082 (https://ru.mouser.com/ProductDetail/KEMET/C0603C104K3RAC7082)
40 | C41, C42 | C0603C270J5GAC7411 | D (https://content.kemet.com/datasheets/KEM_C1003_C0G_SMD.pdf) | KEMET | SMD0603 | Ceramic 27pF 5% NP0 50V | 2 | 0.23 | 0.460 |  | 399-C0603C270J5GAC7411CT-ND (https://www.digikey.com/en/products/detail/kemet/C0603C270J5GAC7411/12701403) | 80-C0603C270J5GACLR (https://ru.mouser.com/ProductDetail/KEMET/C0603C270J5GAC7411)
41 | C50-C69 | EEU-FC2A681 | D (https://industrial.panasonic.com/cdbs/www-data/pdf/RDF0000/ABA0000C1209.pdf) | Panasonic | Radial, T/H 40.0x18.0 | Capacitor Aluminum Electrolytic Radial 680µF 100V 36mOhm 5000h | 20 | 4.81 | 96.200 |  | P10875-ND (https://www.digikey.com/en/products/detail/panasonic-electronic-components/EEU-FC2A681/285738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) | 667-EEU-FC2A681 (https://ru.mouser.com/ProductDetail/Panasonic/EEU-FC2A681)
42 | C70-C79 | C2220C105KARACTU | D (https://content.kemet.com/datasheets/KEM_C1011_X7R_TIP_RING_SMD.pdf) | KEMET | SMD2220 | Ceramic 1uF 10% X7R 250V | 10 | 5 | 50.000 |  | 399-4690-1-ND (https://www.digikey.com/en/products/detail/kemet/C2220C105KARACTU/992183) | 80-C2220C105KAR (https://ru.mouser.com/ProductDetail/KEMET/C2220C105KARACTU)
43 | C89, C90, C104, C107, C120, C123, C132, C133 | C1608X5R1E225K080AB | D (https://product.tdk.com/en/system/files) | TDK | SMD0603 | Ceramic 2.2uF 10% X5R 25V | 8 | 0.37 | 2.960 |  | 445-5964-1-ND (https://www.digikey.com/en/products/detail/tdk-corporation/C1608X5R1E225K080AB/2443442) | 810-C1608X5R1E225K (https://ru.mouser.com/ProductDetail/TDK/C1608X5R1E225K080AB)
44 | C96, C97, C112, C113 | CGA8M1C0G3F221K200KA | D (https://product.tdk.com/en/system/files) | TDK | SMD1812 | Ceramic 220pF 10% NP0 3kV | 4 | 1.44 | 5.760 |  | 445-13094-1-ND (https://www.digikey.com/en/products/detail/tdk-corporation/CGA8M1C0G3F221K200KA/3950330) | 810-CGA8M1C0G3F221KA (https://ru.mouser.com/ProductDetail/TDK/CGA8M1C0G3F221K200KA)
45 | C98, C99, C114, C115 | GRM1885C1H100JA01D | D (https://www.murata.com/-/media/webrenewal/support/library/catalog/products/capacitor/ceramiccapacitor/c02e.ashx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) | Murata | SMD0603 | Ceramic 10pF 5% NP0 50V | 4 | 0.2 | 0.800 |  | 490-1403-1-ND (https://www.digikey.com/en/products/detail/murata-electronics/GRM1885C1H100JA01D/586930) | 81-GRM39C100D50 (https://ru.mouser.com/ProductDetail/Murata-Electronics/GRM1885C1H100JA01D)
 | R e s i s t o r
46 | R1,R4, R7, R11, R13, R24, R28, R41, R42, R44, R46, R54, R57, R58, R61, R76, R77, R78, R79, R80, R81, R83, R85, R86, R99, R102, R113, R116, R119, R120 | ERJ-3EKF1002V | D (https://industrial.panasonic.com/cdbs/www-data/pdf/RDA0000/AOA0000C304.pdf) | Panasonic | SMD0603 | 10kOhm 1% 100ppm 0.1W | 30 | 0.1 | 3.000 |  | P10.0KHCT-ND (https://www.digikey.com/product-detail/en/panasonic-electronic-components/ERJ-3EKF1002V/P10-0KHCT-ND/198102) | 667-ERJ-3EKF1002V (https://ru.mouser.com/ProductDetail/Panasonic/ERJ-3EKF1002V)
47 | R2, R3, R6, R8, R12, R14, R16, R17, R21, R22, R23, R27, R32, R35, R38, R39, R43, R55, R68, R74, R75, R89, R90, R91, R92, R103, R104, R105, R106 | ERJ-3EKF1001V | D (https://industrial.panasonic.com/cdbs/www-data/pdf/RDA0000/AOA0000C304.pdf) | Panasonic | SMD0603 | 1kOhm 1% 100ppm 0.1W | 29 | 0.1 | 2.900 |  | P1.00KHCT-ND (https://www.digikey.com/product-detail/en/panasonic-electronic-components/ERJ-3EKF1001V/P1-00KHCT-ND/198071) | 667-ERJ-3EKF1001V (https://ru.mouser.com/ProductDetail/Panasonic/ERJ-3EKF1001V)
48 | R5, R15, R26, R33 | non |  |  | SMD0603 |  | 4 |  | 0.000
49 | R9, R10, R18, R20, R29, R30, R31 | ERJ-3EKF10R0V | D (https://industrial.panasonic.com/cdbs/www-data/pdf/RDA0000/AOA0000C304.pdf) | Panasonic | SMD0603 | 10Ohm 1% 100ppm 0.1W | 7 | 0.1 | 0.700 |  | P10.0HCT-ND (https://www.digikey.com/en/products/detail/panasonic-electronic-components/ERJ-3EKF10R0V/196065) | 667-ERJ-3EKF10R0V (https://ru.mouser.com/ProductDetail/Panasonic/ERJ-3EKF10R0V)
50 | R19, R37, R51, R52, R56, R59, R65, R66 | ERJ-3EKF2000V | D (https://industrial.panasonic.com/cdbs/www-data/pdf/RDA0000/AOA0000C304.pdf) | Panasonic | SMD0603 | 200Ohm 1% 100ppm 0.1W | 8 | 0.1 | 0.800 |  | P200HCT-ND (https://www.digikey.com/en/products/detail/panasonic-electronic-components/ERJ-3EKF2000V/196205) | 667-ERJ-3EKF2000V (https://ru.mouser.com/ProductDetail/Panasonic/ERJ-3EKF2000V)
51 | R25, R36, R40, R45, R47, R49, R50, R53, R63, R64, R67, R73, R82, R84, R93, R94, R107, R108, R117 | ERJ-3EKF1000V | D (https://industrial.panasonic.com/cdbs/www-data/pdf/RDA0000/AOA0000C304.pdf) | Panasonic | SMD0603 | 100Ohm 1% 100ppm 0.1W | 19 | 0.1 | 1.900 |  | P100HCT-ND (https://www.digikey.com/product-detail/en/panasonic-electronic-components/ERJ-3EKF1000V/P100HCT-ND/198109) | 667-ERJ-3EKF1000V (https://ru.mouser.com/ProductDetail/Panasonic/ERJ-3EKF1000V)
52 | R34 | ERJ-U03J105V | D (https://industrial.panasonic.com/cdbs/www-data/pdf/RDP0000/AOA0000C334.pdf) | Panasonic | SMD0603 | 1MOhm 5% 200ppm 0.1W | 1 | 0.1 | 0.100 |  | 10-ERJ-U03J105VCT-ND (https://www.digikey.com/en/products/detail/panasonic-electronic-components/ERJ-U03J105V/11636001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) | 667-ERJ-U03J105V (https://ru.mouser.com/ProductDetail/Panasonic/ERJ-U03J105V)
53 | R48 | ERJ-3EKF1801V | D (https://industrial.panasonic.com/cdbs/www-data/pdf/RDA0000/AOA0000C304.pdf) | Panasonic | SMD0603 | 1.8kOhm 1% 100ppm 0.1W | 1 | 0.1 | 0.100 |  | P1.80KHCT-ND (https://www.digikey.com/en/products/detail/panasonic-electronic-components/ERJ-3EKF1801V/1746325) | 667-ERJ-3EKF1801V (https://ru.mouser.com/ProductDetail/Panasonic/ERJ-3EKF1801V)
54 | R60 | ERJ-3EKF2202V | D (https://industrial.panasonic.com/cdbs/www-data/pdf/RDA0000/AOA0000C304.pdf) | Panasonic | SMD0603 | 22kOhm 1% 100ppm 0.1W | 1 | 0.1 | 0.100 |  | P22.0KHCT-ND (https://www.digikey.com/en/products/detail/panasonic-electronic-components/ERJ-3EKF2202V/1746336) | 667-ERJ-3EKF2202V (https://ru.mouser.com/ProductDetail/Panasonic/ERJ-3EKF2202V)
55 | R62 | ERJ-3EKF4302V | D (https://industrial.panasonic.com/cdbs/www-data/pdf/RDA0000/AOA0000C304.pdf) | Panasonic | SMD0603 | 43kOhm 1% 100ppm 0.1W | 1 | 0.1 | 0.100 |  | P43.0KHCT-ND (https://www.digikey.com/en/products/detail/panasonic-electronic-components/ERJ-3EKF4302V/1746411) | 667-ERJ-3EKF4302V (https://ru.mouser.com/ProductDetail/Panasonic/ERJ-3EKF4302V)
56 | R69, R70, R71, R72 | ERJ-3EKF3301V | D (https://industrial.panasonic.com/cdbs/www-data/pdf/RDA0000/AOA0000C304.pdf) | Panasonic | SMD0603 | 3.3kOhm 1% 100ppm 0.1W | 4 | 0.1 | 0.400 |  | P3.30KHCT-ND (https://www.digikey.com/en/products/detail/panasonic-electronic-components/ERJ-3EKF3301V/1746376) | 667-ERJ-3EKF3301V (https://ru.mouser.com/ProductDetail/Panasonic/ERJ-3EKF3301V)
57 | R87, R88, R122, R123 | ERJ-3EKF5101V | D (https://industrial.panasonic.com/cdbs/www-data/pdf/RDA0000/AOA0000C304.pdf) | Panasonic | SMD0603 | 5.1kOhm 1% 100ppm 0.1W | 4 | 0.1 | 0.400 |  | P5.10KHCT-ND (https://www.digikey.com/en/products/detail/panasonic-electronic-components/ERJ-3EKF5101V/1746427) | 667-ERJ-3EKF5101V (https://ru.mouser.com/ProductDetail/Panasonic/ERJ-3EKF5101V)
58 | R95, R95A, R96, R96A, R97, R97A, R98, R98A, R109, R109A, R110, R110A, R111, R111A, R112, R112A | ERJ-6RQF1R0V | D (https://industrial.panasonic.com/cdbs/www-data/pdf/RDN0000/AOA0000C313.pdf) | Panasonic | SMD0603 | 1Ohm 1% 100ppm 0.1W | 16 | 0.32 | 5.120 |  | P1.0DCT-ND (https://www.digikey.com/en/products/detail/panasonic-electronic-components/ERJ-6RQF1R0V/250172) | 667-ERJ-6RQF1R0V (https://ru.mouser.com/ProductDetail/Panasonic/ERJ-6RQF1R0V)
59 | R100, R100A, R100B, R100C, R101, R101A, R101B, R101C, R114, R114A, R114B, R114C, R115, R115A, R115B, R115C | ERJ-1TYJ510U | D (https://media.digikey.com/pdf/Data%20Sheets/Panasonic%20Resistors%20Thermistors%20PDFs/ERJ-xG,14,12(Z),1T_Rev_Apr_2015.pdf) | Panasonic | SMD2512 | 51Ohm 5% 200ppm 1W | 16 | 0.32 | 5.120 |  | PT51XCT-ND (https://www.digikey.com/en/products/detail/panasonic-electronic-components/ERJ-1TYJ510U/365222) | 667-ERJ-1TYJ510U (https://ru.mouser.com/ProductDetail/Panasonic/ERJ-1TYJ510U)
60 | R118 | CSSH2728FT5L00 | D (https://www.seielect.com/catalog/sei-css_cssh.pdf) | Stackpole | SMD2728 | 5mOhms 1% 25ppm 4W | 1 | 1 | 1.000 |  | CSSH2728FT5L00CT-ND (https://www.digikey.com/en/products/detail/stackpole-electronics-inc/CSSH2728FT5L00/1923229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) | -
61 | R121 | ERJ-6GEY0R00V | D (https://industrial.panasonic.com/cdbs/www-data/pdf/RDA0000/AOA0000C301.pdf) | Panasonic | SMD0805 | 0Ohm | 1 | 0.1 | 0.100 |  | P0.0ACT-ND (https://www.digikey.com/en/products/detail/panasonic-electronic-components/ERJ-6GEY0R00V/78163) | 667-ERJ-6GEY0R00V (https://ru.mouser.com/ProductDetail/Panasonic/ERJ-6GEY0R00V)
62 | RT1, RT2, RT3, RT4 | B57861S0103J040 | D (https://www.tdk-electronics.tdk.com/inf/50/db/ntc/NTC_Mini_sensors_S861.pdf) | TDK-EPCOS | T/H | NTC resistor 10kOhm 5% 3988K | 4 | 1.89 | 7.560 |  | 495-75200-ND (https://www.digikey.com/en/products/detail/epcos-tdk-electronics/B57861S0103J040/3500452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) | 871-B57861S103J40 (https://ru.mouser.com/ProductDetail/EPCOS-TDK/B57861S0103J040)
 | C o n n e c t o r
63 | X1 | 0039281043 | D (https://www.molex.com/pdm_docs/sd/039281043_sd.pdf) | Molex | T/H | Connector Header 4 pin, 4.2mm | 1 | 1.92 | 1.920 |  | WM3801-ND (https://www.digikey.com/en/products/detail/molex/0039281043/61400) | 538-39-28-1043 (https://ru.mouser.com/ProductDetail/Molex/39-28-1043?qs=LQQHZ4xw2XCMHoV0KRLGhg%3D%3D)
64 | X2, X4 | WF-2R | D (https://static.chipdip.ru/lib/143/DOC006143808.pdf) | Connfly | T/H | Connector 2 pin, Right angle, 2.54mm | 2 | 0.07 | 0.140 |  | - | - | ChipDip (https://www.chipdip.ru/product/wf-2r)
65 | X3, X5 | SMA-J-P-H-RA-TH1 | D (http://suddendocs.samtec.com/catalog_english/sma.pdf) | Samtec | T/H | SMA Jack, Socket, Right Angle 50Ohm | 2 | 7 | 14.000 |  | SAM8856-ND (https://www.digikey.com/en/products/detail/samtec-inc/SMA-J-P-H-RA-TH1/2664715) | 200-SMAJPHRATH1 (https://ru.mouser.com/ProductDetail/Samtec/SMA-J-P-H-RA-TH1)
66 | X6 | 1074 | D (http://www.keystoneelectronics.net/ENG._DEPT/WEB_ORACLE/PDF/PDF%20CAT%20NO%20DRAWINGS/1000-1999/1074.PDF) | Keystone | T/H | Battery holder for CR2032 | 1 | 1.09 | 1.090 |  | 36-1074-ND (https://www.digikey.com/en/products/detail/keystone-electronics/1074/9921784) | 534-1074 (https://ru.mouser.com/ProductDetail/Keystone-Electronics/1074?qs=u16ybLDytRZ%2FZj7HSRmD5g%3D%3D)
67 | X7 | PLS2-5 | D (https://static.chipdip.ru/lib/245/DOC000245332.pdf) | Connfly | T/H | Connector Header 5 pin, 2mm | 1 | 0.05 | 0.050 | SWD connector | - | - | ChipDip (https://www.chipdip.ru/product/ds1025-01-1-5-p8bv1-pls2-5-pls2-05)
68 | X8 | SS-52400-003 | D (https://belfuse.com/resources/drawings/stewartconnector/dr-stw-ss-52400-003.pdf) | Stewart | SMD+T/H | USB Type-C, Right Angle Receptacle 24 Position | 1 | 3.5 | 3.500 |  | 380-SS-52400-003CT-ND (https://www.digikey.com/en/products/detail/stewart-connector/SS-52400-003/11205655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) | 530-SS-52400-003 (https://ru.mouser.com/ProductDetail/Stewart-Connector-Bel/SS-52400-003)
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

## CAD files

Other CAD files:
discharge_chambers/Rotating Arc.f3d
power_electronics/transformer/High-Voltage_Transformer.f3d

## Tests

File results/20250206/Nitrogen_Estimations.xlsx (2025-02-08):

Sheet: Sheet1
 |  | ppm | NOx/N | mg/L |  |  |  |  |  |  | Basic pH |  | 6.8
 |  | 500
Nitrit | NO2- | 100 | 0.30 | 30.43478261 | Type | DBD |  |  |  |  | pH | H+ | ΔH+ | M
Nitrat | NO3- | 400 | 0.23 | 90.32258065 |  |  |  |  |  |  | 6.80 | 1.584893192e-07 | 0 | 58.8 | 0.009319171972 | 0
Total |  |  |  | 120.7573633 |  |  |  |  |  |  | 6.70 | 1.995262315e-07 | 4.103691225e-08 | 58.8 | 0.01173214241 | 0.00241297044
Volume | 5 | l |  |  |  |  |  |  |  |  | 6.60 | 2.511886432e-07 | 9.26993239e-08 | 58.8 | 0.01476989222 | 0.005450720246
N | 0.6 | g | 3622.720898 |  |  |  |  |  |  |  | 6.50 | 3.16227766e-07 | 1.577384468e-07 | 58.8 | 0.01859419264 | 0.00927502067
 |  |  |  |  |  |  |  |  |  |  | 6.40 | 3.981071706e-07 | 2.396178513e-07 | 58.8 | 0.02340870163 | 0.01408952966
Time | 10 | min |  |  |  |  |  |  |  |  | 6.30 | 5.011872336e-07 | 3.426979144e-07 | 58.8 | 0.02946980934 | 0.02015063737
Power | 0.3 | kW |  |  |  |  |  |  |  |  | 6.20 | 6.309573445e-07 | 4.724680252e-07 | 58.8 | 0.03710029186 | 0.02778111988
 |  |  |  |  |  |  |  |  |  |  | 6.10 | 7.943282347e-07 | 6.358389155e-07 | 58.8 | 0.0467065002 | 0.03738732823
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

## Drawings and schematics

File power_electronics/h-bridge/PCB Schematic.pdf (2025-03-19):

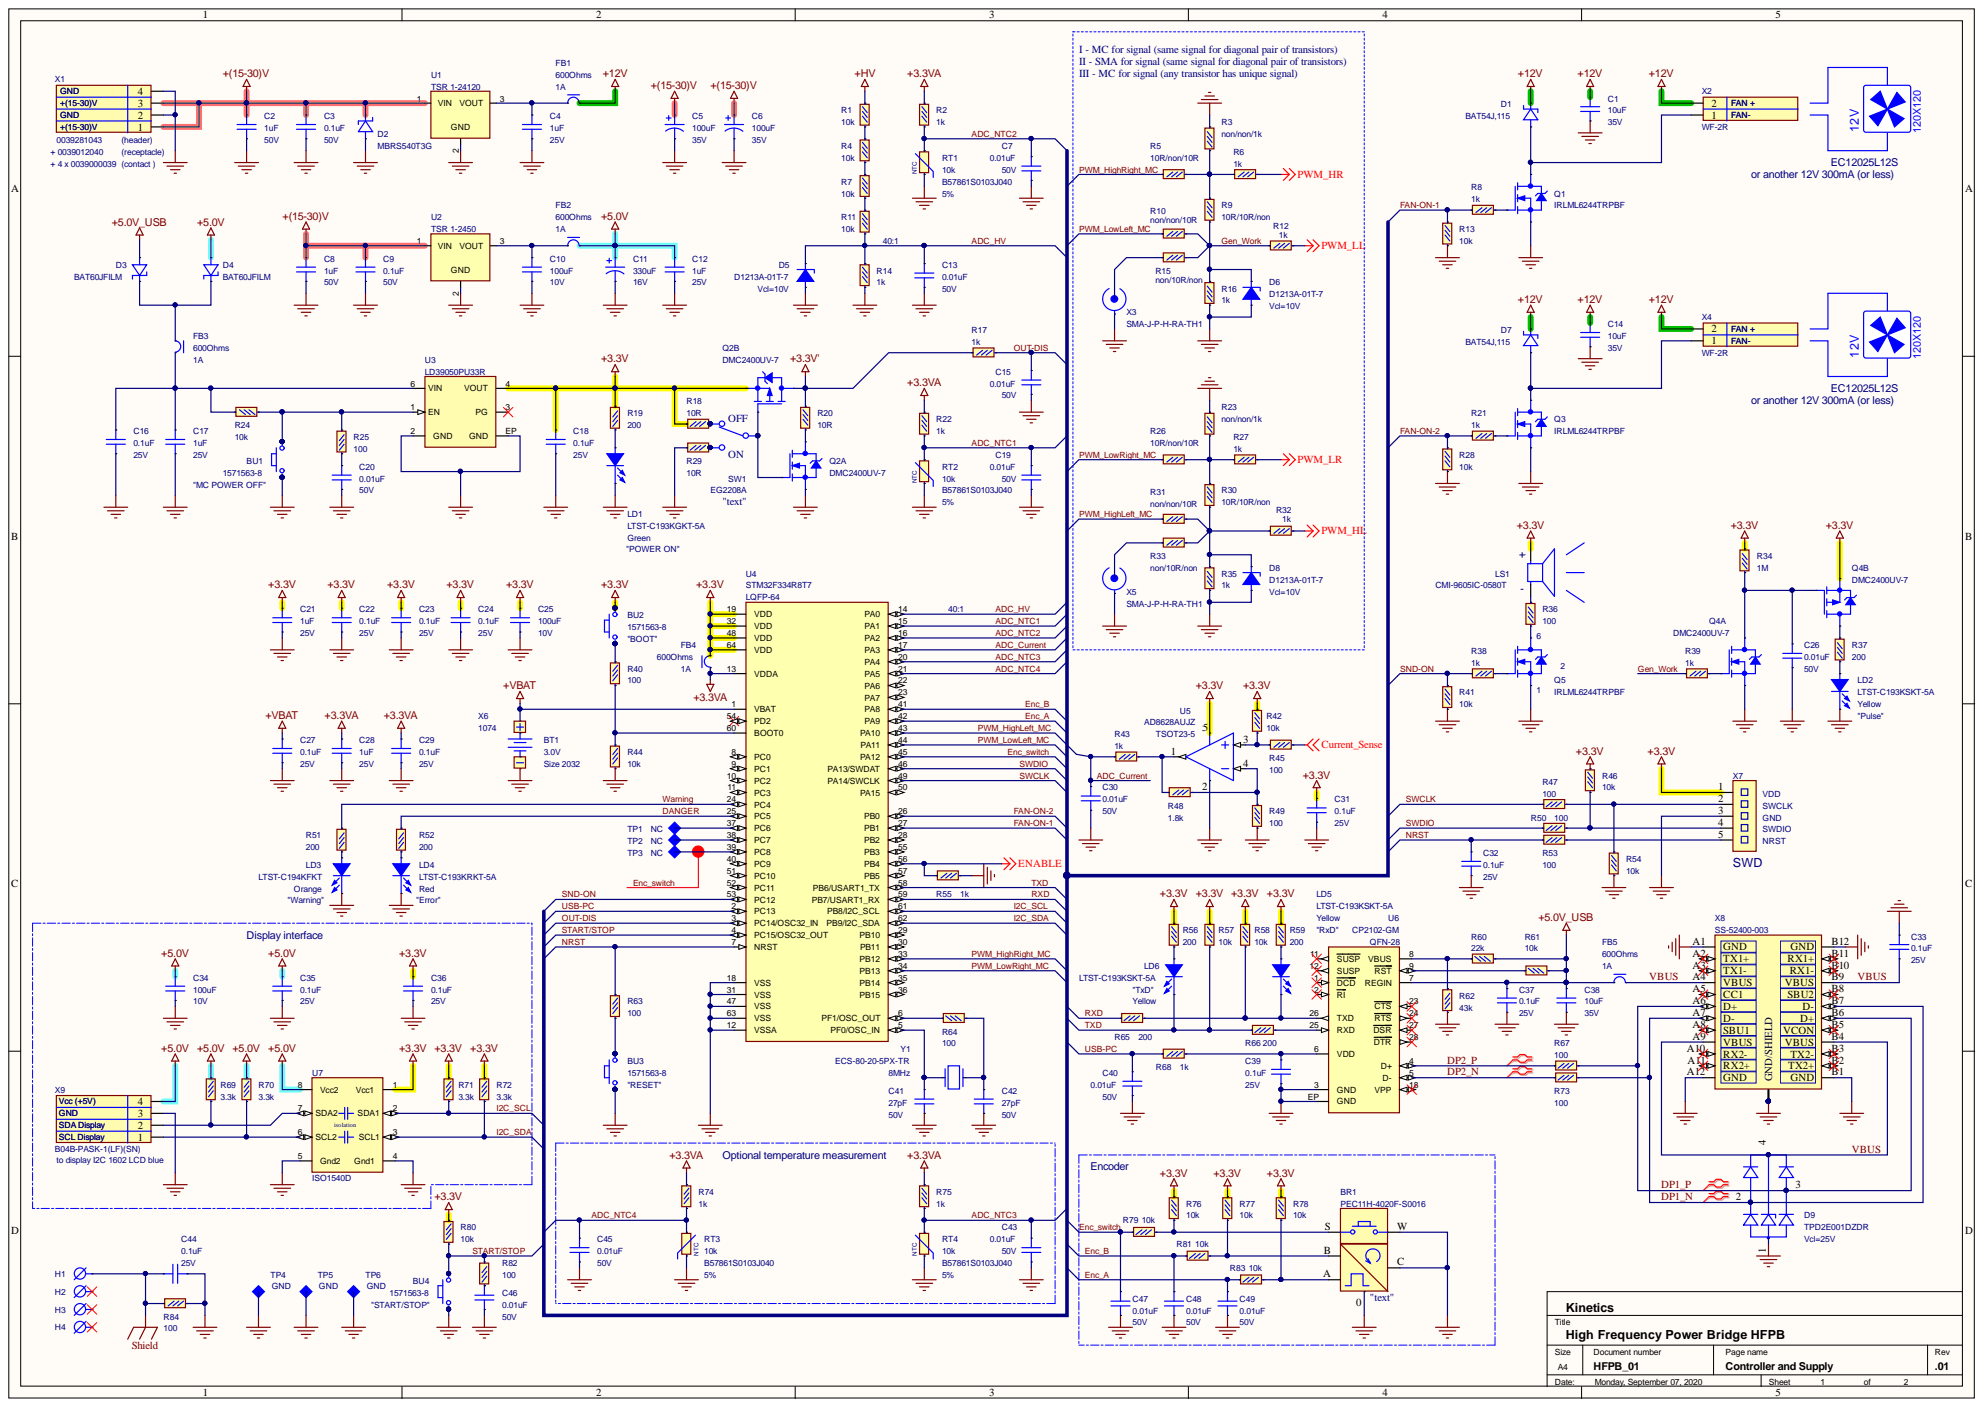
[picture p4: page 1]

I - MC for signal (same signal for diagonal pair of transistors)
II - SMA for signal (same signal for diagonal pair of transistors)
III - MC for signal (any transistor has unique signal)

or another 12V 300mA (or less)

2 | FAN +
1 | FAN-

Vcc (+5V) | 4
GND | 3
SDA Display | 2
SCL Display | 1

B04B-PASK-1(LF)(SN)
to display I2C 1602 LCD blue

+3.3VA | Optional temperature measurement +3.3VA

Title
High Frequency Power Bridge HFPB

Size A4 | Document number HFPB_01 | Page name Controller and Supply | Rev .01

Date: Monday, September 07, 2020 | Sheet 1 of 2

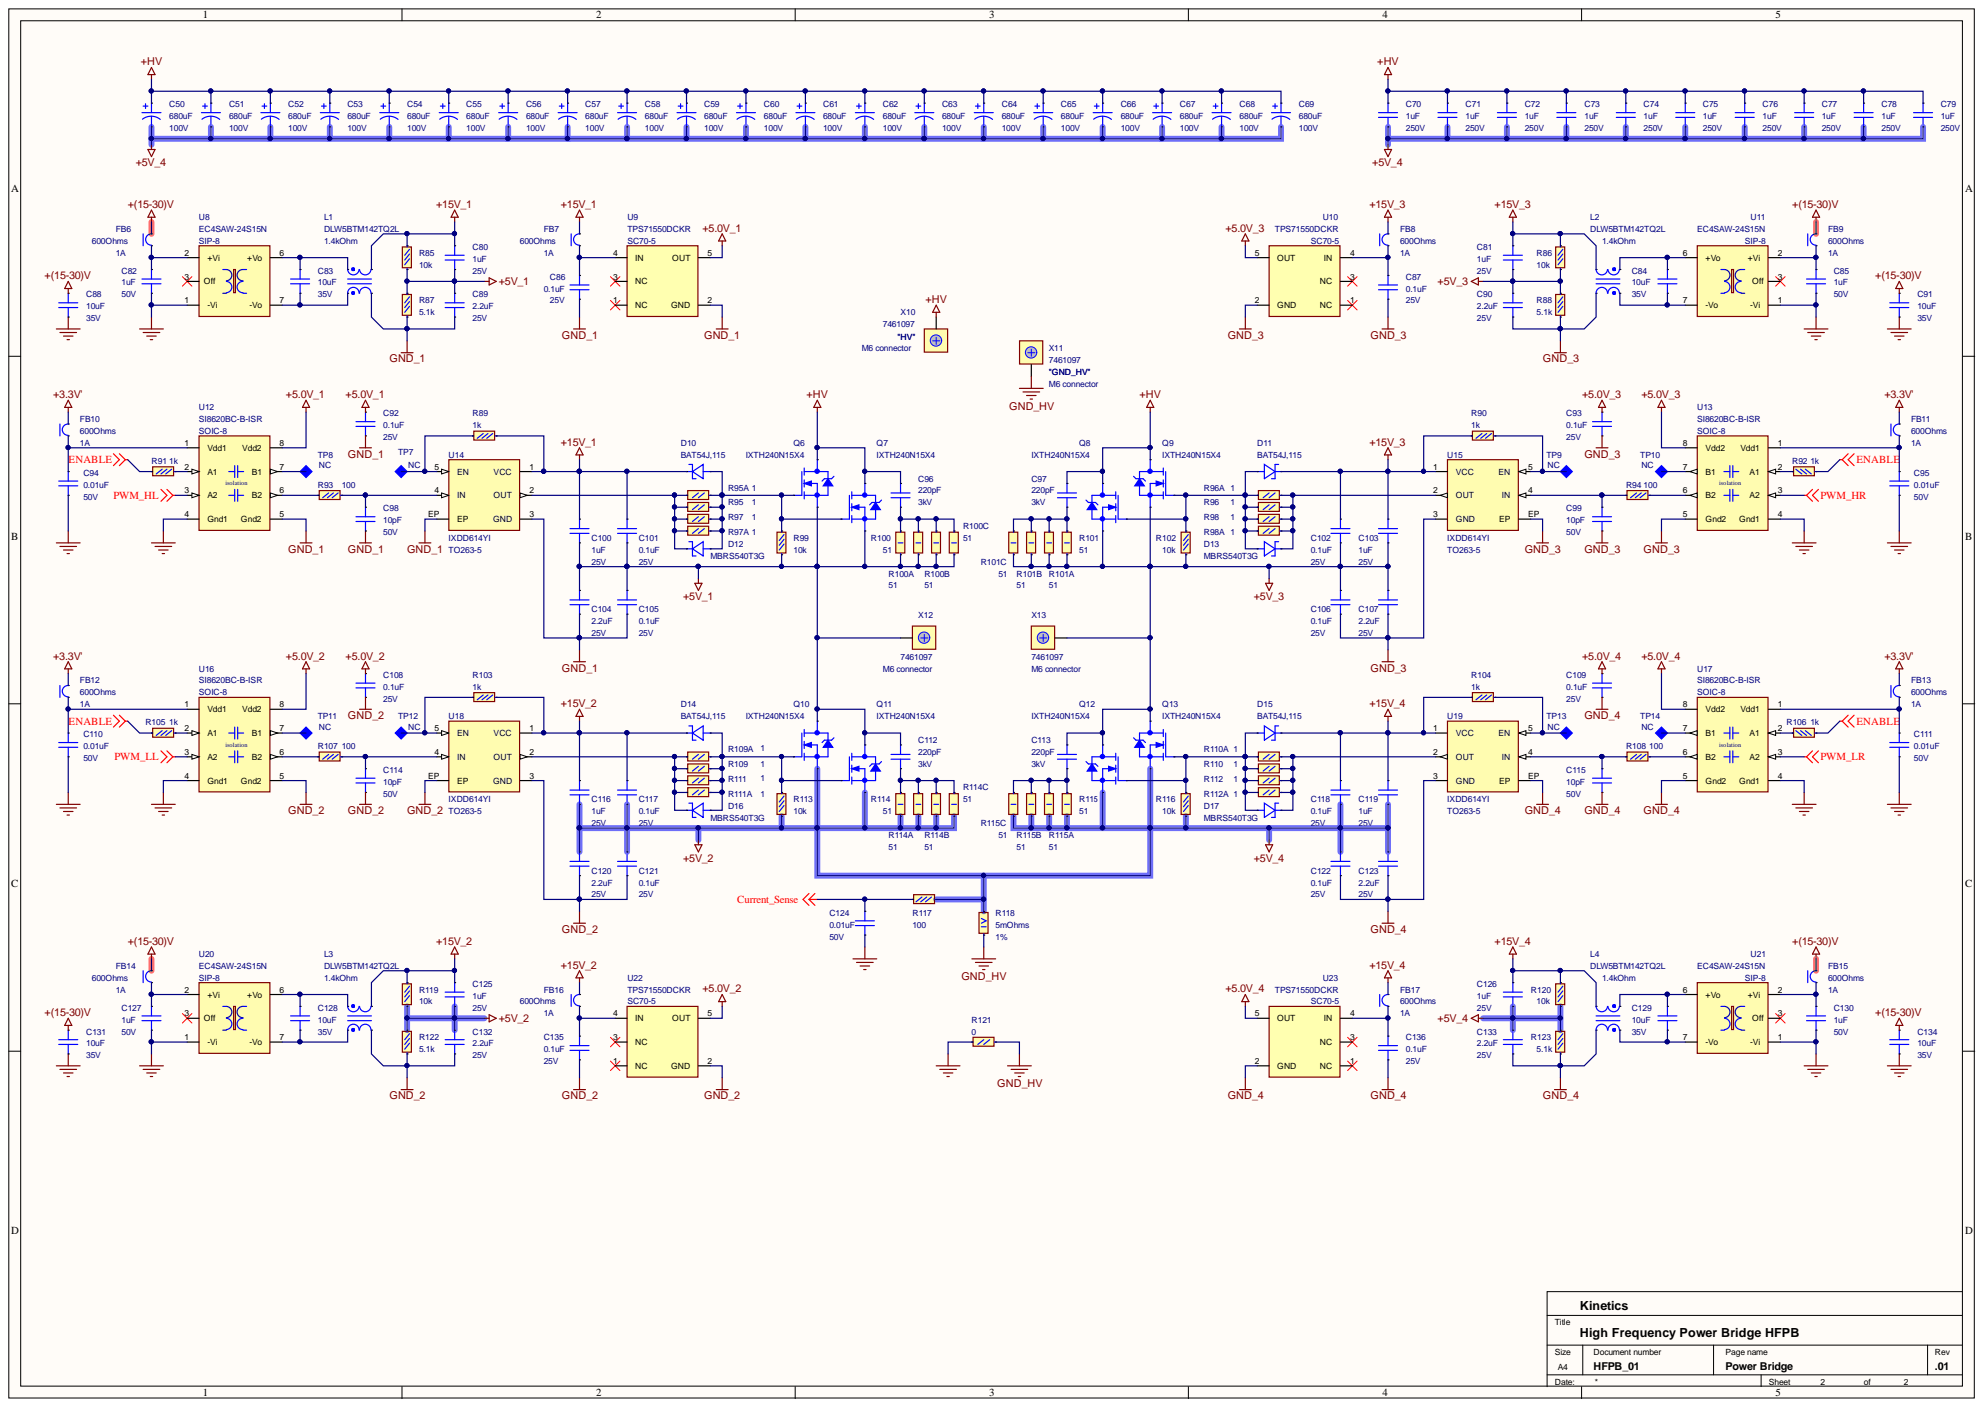
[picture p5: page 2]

Title
High Frequency Power Bridge HFPB

Size A4 | Document number HFPB_01 | Page name Power Bridge | Rev .01

Date: * | Sheet 2 of 2

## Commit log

2025-02-06 first commit - project describtion
    [Nitrogen_Estimations.xlsx]
2025-02-08 add MIT License and authors
    [Nitrogen_Estimations.xlsx]
2025-03-08 some additional explanation of electron energy in wet air
    [rotational_levels_N2_O2.xlsx]
2025-03-09 Discharge Chambers
    [Cylindric_Gliding_Arc.f3d, Spiral_Gliging_Arc.f3d]
2025-03-19 add power electronics
    [BOM.xlsx, HFPB_01, PAGE-1.SchDoc, HFPB_01, PAGE-2.SchDoc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]
2026-01-23 dischange chambers update
    [Cylindric_Gliding_Arc.f3d, Rotating Arc.f3d, Spiral_Gliging_Arc.f3d]
